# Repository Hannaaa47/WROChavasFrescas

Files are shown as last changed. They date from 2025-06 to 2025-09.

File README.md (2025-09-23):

<div align="center">

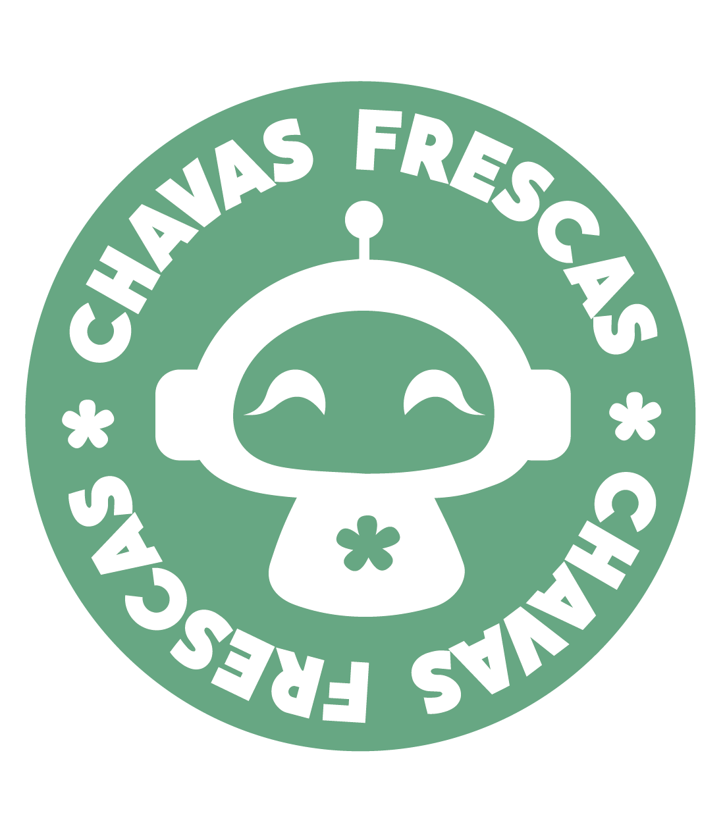
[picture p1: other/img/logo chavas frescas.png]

</div> 

<br>

En este repositorio nuestro equipo "Chavas frescas" desglosaremos como logramos crear un robot para participar en la World Robot Olympiad en la categoria de Future Engineers.

&nbsp;

# Tabla de contenidos
* **[Contenido del repositorio](#contenido-del-repositorio)**
* **[¿En que consiste la competencia?](#en-que-consiste-la-competencia)**
* **[Equipo](#equipo)**
* **[Fotos del robot](#fotos-del-robot)**
* **[Videos del robot](#videos-del-robot)**
* **[Hardware](#hardware)**
  * [Componentes](#componentes)
  * [Reporte de costos](#reporte-de-costos)
* **[Mobility Management](#mobility-management)**
  * [Diseño del chasis](#diseño-del-chasis) 
  * [Elección de motores](#eleccion-de-motores) 
* **[Power and Sense Management](#power-and-sense-management)**
  * [Voltaje y amperaje](#voltaje-y-amperaje) 
  * [Esquema](#esquema) 
  * [Sensores](#sensores) 
* **[Software](#software)**

&nbsp;

# Contenido del repositorio
  
*  [`models`](models) — contiene los modelos 3D de nuestro robot.

*  [`other`](other) — contiene imagenes y archivos que ayudan a entender más a fondo como preparar el robot para la competencia, contiene datasheets y imagenes de los componentes.

*  [`schemes`](schemes) — contiene el esquema de conexiones del robot y un diagrama de flujo del codigo.

*  [`src`](src) — contiene el codigo de nuestro robot.

*  [`t-photos`](t-photos) — continene fotos de los integrantes del equipo.

*  [`v-photos`](v-photos) — contiene seis fotos del carrito.

*  [`videos`](videos) — contiene un link para un video del robot.

&nbsp;

# ¿En que consiste la competencia?

La World Robot Olympiad es una competencia mundial de robótica que busca una competencia sana para jóvenes, alentando el aprendizaje y la curiosidad.

En nuestro caso participamos en la categoría de Future Engineers, el objetivo es construir un vehículo autodirigido con algunas limitaciones(como peso, tamaño y número de motores), el cual debe de ser capaz de pasar dos pruebas.

Prueba abierta.
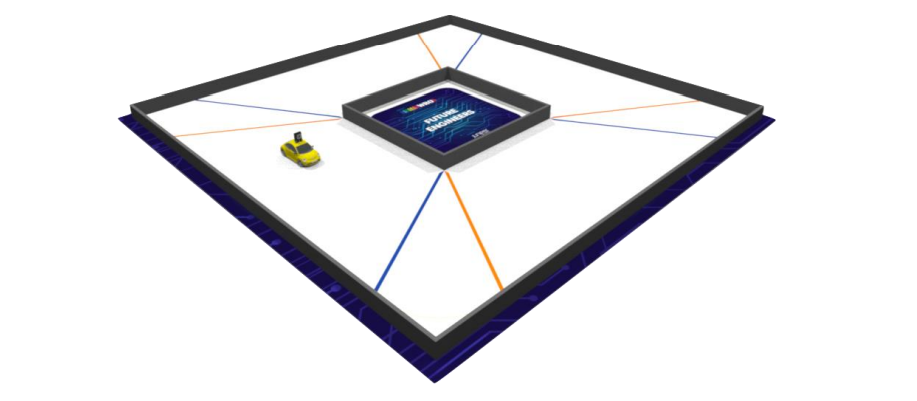
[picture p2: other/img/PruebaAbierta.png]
Prueba abierta


Prueba de obstáculos. 
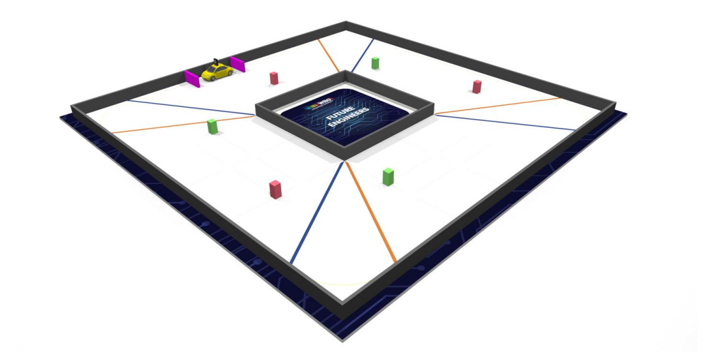
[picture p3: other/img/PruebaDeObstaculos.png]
Prueba de obstáculos


En la prueba abierta nuestro vehículo debe completar exitosamente tres vueltas a la pista. En la prueba de obstáculos además de dar tres vueltas a la pista el robot debe de ir esquivando obstáculos y al final estacionarse en paralelo. En ambas pruebas existen elementos aleatorios como la posición de los obstáculos y el sentido de las vueltas, estos elementos cambian después de cada ronda. Para conocer más puede leer las [reglas generales](https://wro-association.org/wp-content/uploads/WRO-2022-Future-Engineers-General-Rules.pdf) o visitar el [sitio oficial](https://wromexico.org/). 

&nbsp;

# Equipo

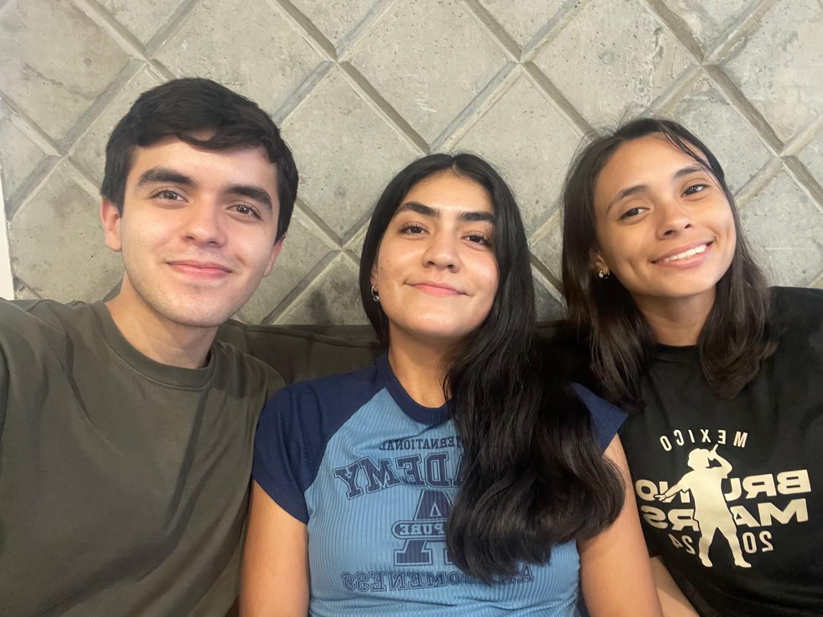
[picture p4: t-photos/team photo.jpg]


Integrantes del equipo:
- Hanna Alejandra Amador Sánchez
- Ilse Marianne Castillo Pimienta
- Yonatan Morales Togo

Asesor:
- Cesar Espinosa Arce
  
&nbsp;

# Fotos del robot

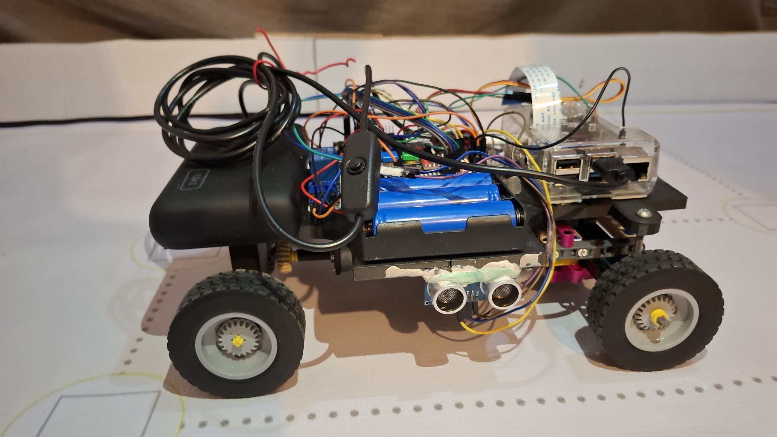
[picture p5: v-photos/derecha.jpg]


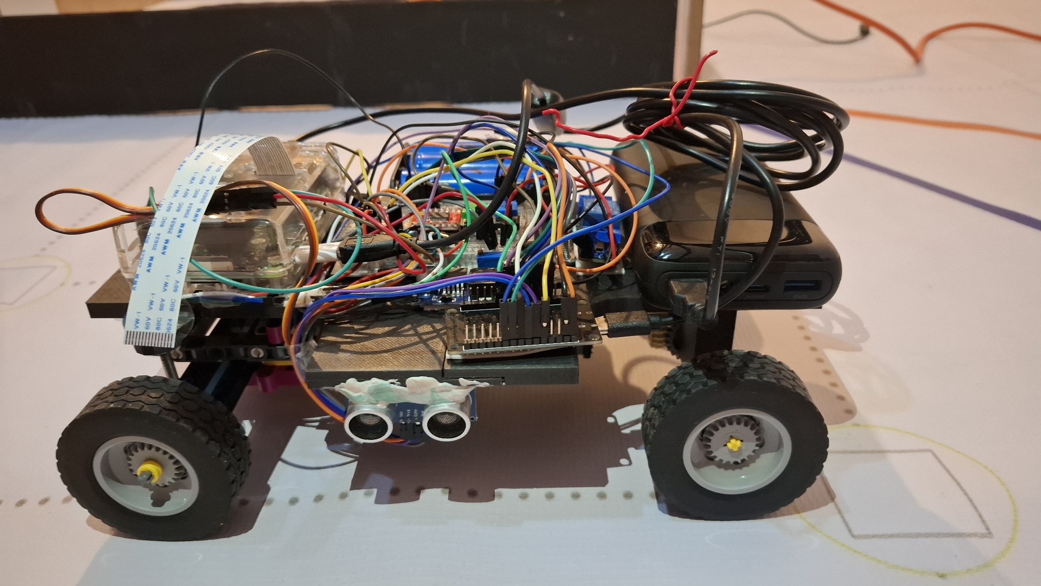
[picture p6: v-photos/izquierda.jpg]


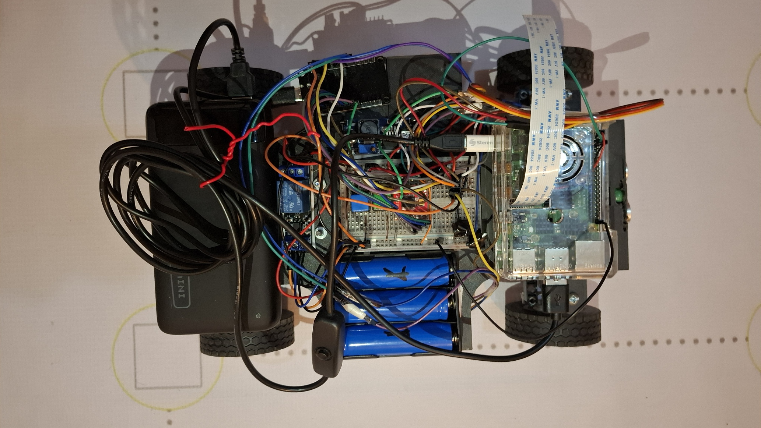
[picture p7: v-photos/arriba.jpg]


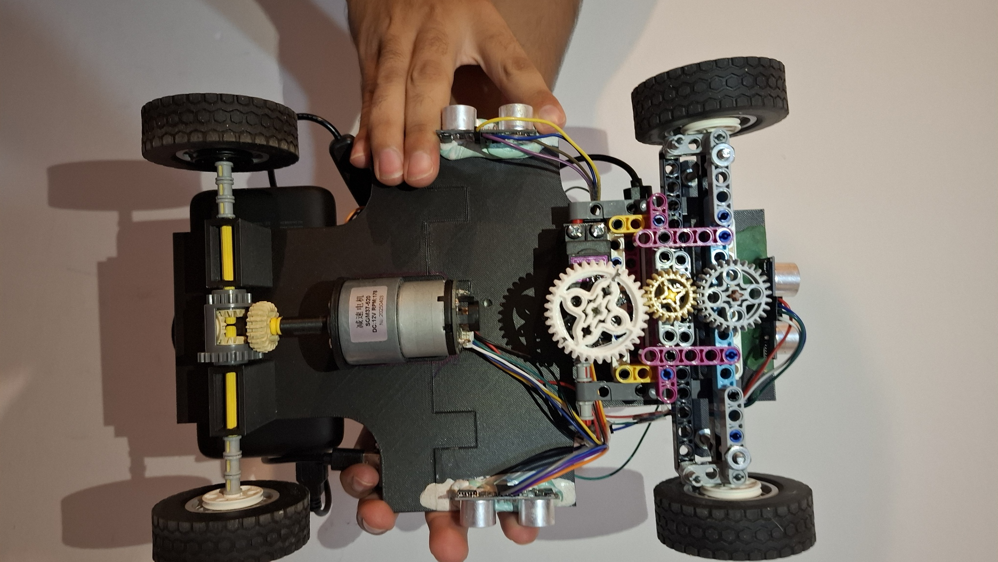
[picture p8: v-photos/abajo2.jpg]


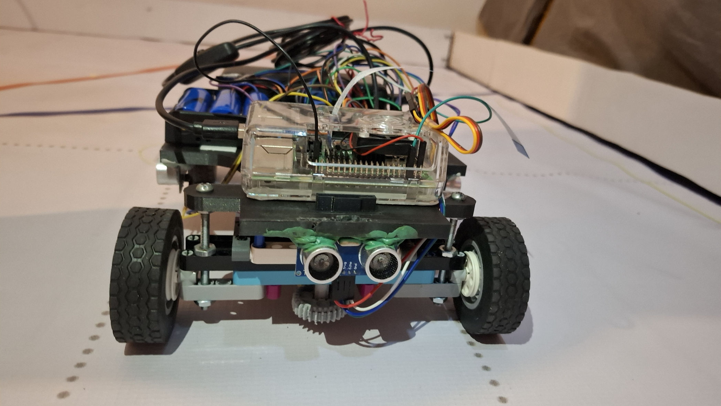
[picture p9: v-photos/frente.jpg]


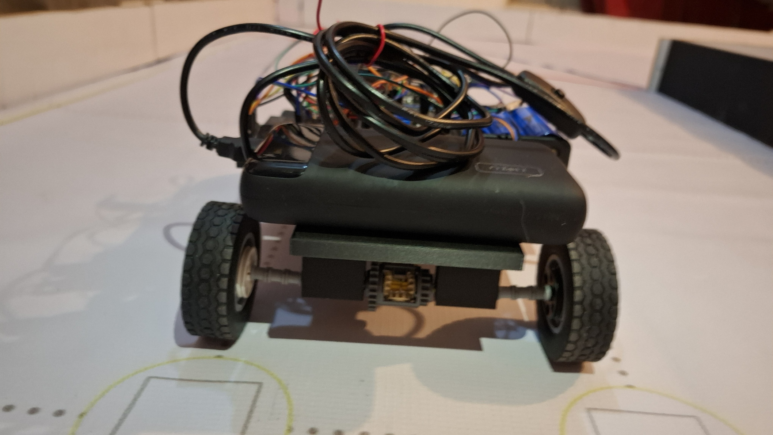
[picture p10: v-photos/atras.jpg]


&nbsp;  

# Videos del robot
Aqui esta el [link](https://youtu.be/UbjT6czdM9U?si=_D7zrM3F1YbVgJT3) para el video de nuestro robot.

# Hardware

## Componentes 

***Esp32*** 

Es un Single Board Microcontroller (SBM), es un sistema en chip (SoC) económico y de bajo consumo que combina funciones Wi-Fi y Bluetooth. Desde una perspectiva técnica, el ESP32 es un MCU de 32 bits con un microprocesador Tensilica Xtensa LX6, con una velocidad de reloj de hasta 240 MHz, 448 KB de ROM y 520 KB de SRAM. También incluye una amplia selección de periféricos, como un ADC de 10 bits, 6x PWM, I₂C, SPI, UART y más. La programación del ESP32 es relativamente sencilla, ya que admite diversos lenguajes de programación, como C/C++, ensamblador y Python. También es compatible con el IDE de Arduino, una popular plataforma de código abierto para la programación de microcontroladores. Para ver mas información puede ver el [datasheet](other/Datasheets/esp32-wrover_datasheet_en.pdf) y la descripción de los [pines GPIO](other/img/ESP32-Pinout.jpg).

Su función en nuestro proyecto es hacer de motor controller y obtener lecturas precisas de los sensores, dada a la rápida comunicación que tiene entre componentes. Elegimos al Esp32 sobre la opción clásica que sería algún arduino, ya que después de analizar ambos llegamos a la conclusión que el Esp32 es mejor. 
<table>
  <tr>
    <td style="width:400px; text-align:center; vertical-align:middle;">
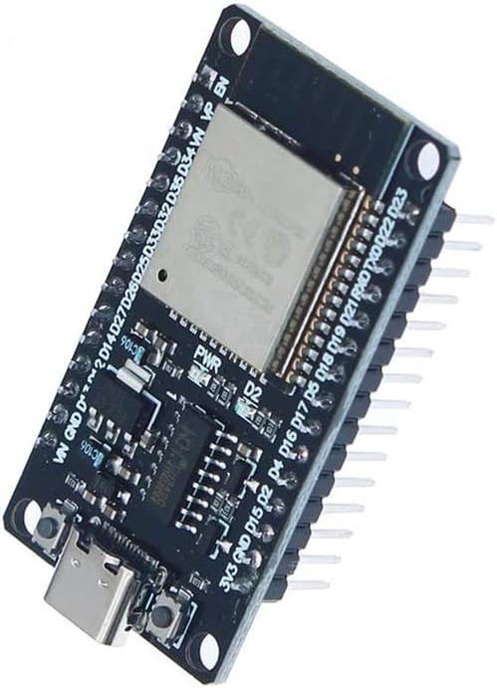
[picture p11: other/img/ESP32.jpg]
ESP32
      
    </td>
    <td style="width:500px; text-align:left; vertical-align:middle;">
      <h3>Especificaciones:</h3>
      <ul>
        <li>Voltaje: 2.3V ~ 3.6V</li>
        <li>Amperaje: 80mA ~ 250mA</li>
      </ul>
    </td>
  </tr>
</table>

<br>

***Raspberry Pi 4 Model B***

El Single-Board Computer (SBC), es un pequeño computador, consiste en una placa base que soporta distintos componentes de un ordenador, como un procesador ARM de hasta 1500 MHz, un chip gráfico y una memoria RAM de hasta 8 GB. Puede ver la configuración de los gpio pines en esta [imagen](other/img/pinesRaspberry.jpg), para ver más información consulte el [datasheet](other/Datasheets/raspberry-pi-4-product-brief.pdf).

Hace la función del cerebro principal del robot, esta a cargo de la computer vision interpretando los datos de la camara, ademas toma las decisiones importantes.

<table>
  <tr>
    <td style="width:400px; text-align:center; vertical-align:middle;">
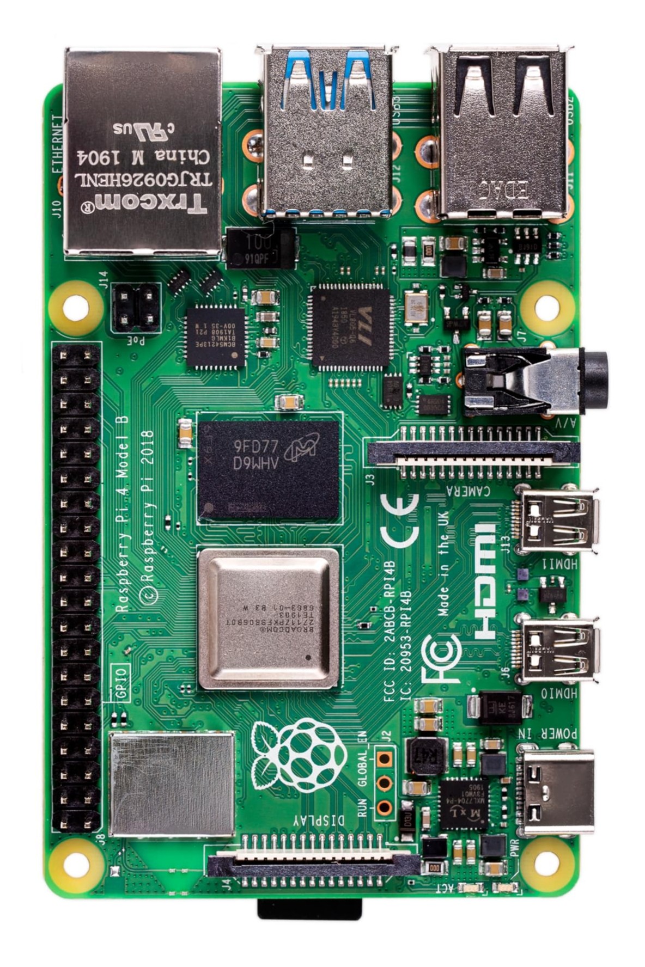
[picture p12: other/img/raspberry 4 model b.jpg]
Raspberry pi
      
    </td>
    <td style="width:500px; text-align:left; vertical-align:middle;">
      <h3>Especificaciones:</h3>
      <ul>
        <li>Voltaje: 5V</li>
        <li>Amperaje: 2500mA ~ 3000mA </li>
      </ul>
    </td>
  </tr>
</table>

<br>

***Servomotor MG995 180°***

Un servomotor es un tipo de motor que permite controlar con precisión la posición, velocidad y aceleración de su eje. A diferencia de un motor eléctrico convencional, un servomotor utiliza un sistema de retroalimentación (como un encoder) para monitorear y corregir continuamente su movimiento, logrando un control más exacto. 

Usamos este servomotor para controlar la dirección del carro, decidimos usar este modelo de servomotor devido a su gran torque. Para más información consulte el [datasheet](other/Datasheets/Servomotor_MG995_datasheet.pdf).

<table>
  <tr>
    <td style="width:400px; text-align:center; vertical-align:middle;">
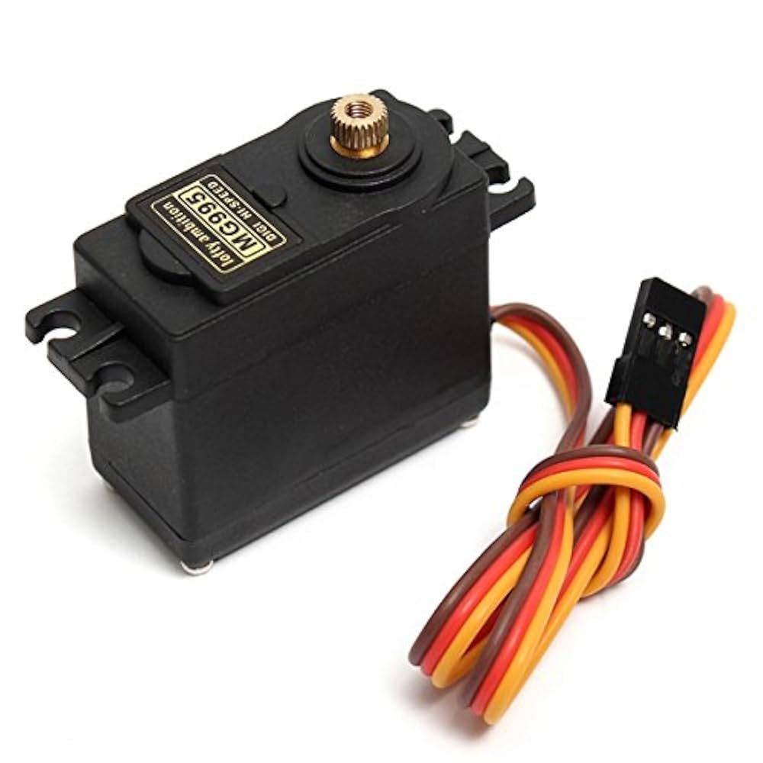
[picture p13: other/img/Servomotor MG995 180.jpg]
Servomotor
      
    </td>
    <td style="width:500px; text-align:left; vertical-align:middle;">
      <h3>Especificaciones:</h3>
      <ul>
        <li>Voltaje:  4.8V - 7.2V</li>
        <li>Amperaje: 200mA ~ 1200mA </li>
        <li>Torque: 9.4kg/cm (4.8V) - 11kg/cm (6V)</li>
      </ul>
    </td>
  </tr>
</table>
  
<br>

***Motor JGB37-520 DC 12v con encoder***

Elegimos un motor de corriente continua, debido a su facilidad para usarlo. Estos motores toman la energía eléctrica mediante corriente continua y la convierten en rotación mecánica. Despues de calcular el [torque](/research/README.md) concluimos que ibamos a necesitar un motor con un buen torque para poder mover el robot. 

Este motor tambien cuenta con un encoder, el encoder nos ayuda a monitorear las el moviemiento del motor.

// gracias a el pudimos implementar un sistema [PID](/research/README.md) para corregir las variaciones de la 
// energia y contar un moviemiento consistente. 
 
 Si quieres saber un poco más del motor revisa esta [imagen](other/Datasheets/motor.webp).

<table>
  <tr>
    <td style="width:400px; text-align:center; vertical-align:middle;">
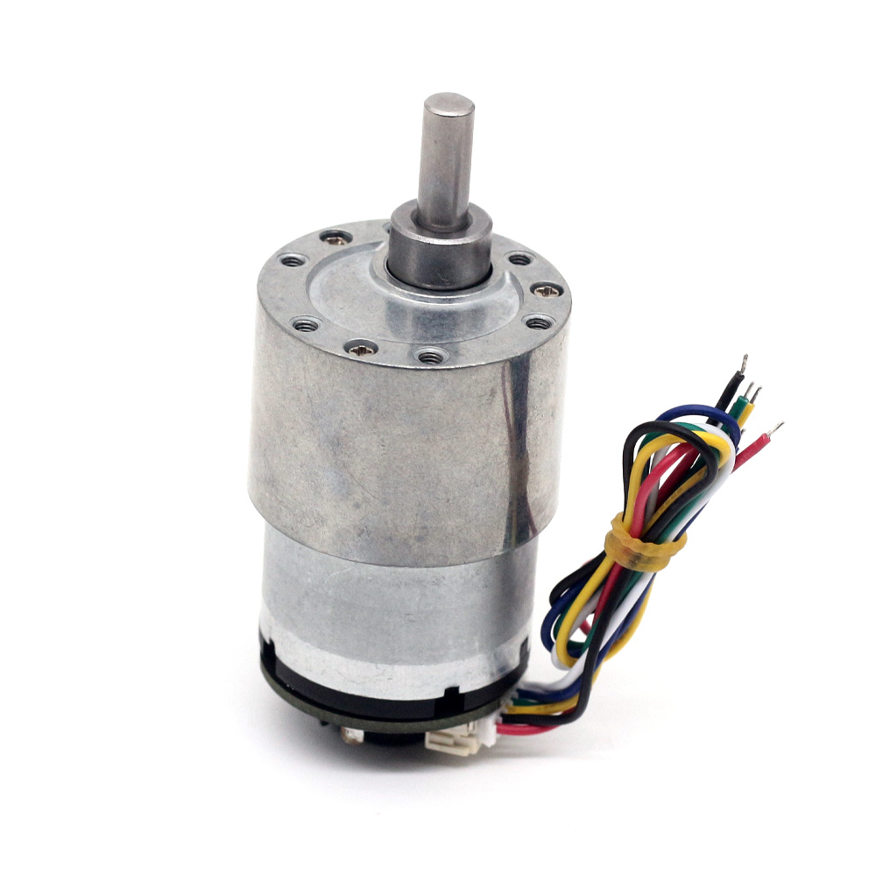
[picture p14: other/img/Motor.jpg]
Motor
      
    </td>
    <td style="width:500px; text-align:left; vertical-align:middle;">
      <h3>Especificaciones:</h3>
      <ul>
        <li>Voltaje:  12V</li>
        <li>Amperaje: 120mA ~ 2300mA </li>
        <li>Torque: 6.5kg.cm (120mA) - 9kg.cm (2300mA)</li>
        <h3>Encoder</h3>
        <li>Voltaje: 3.3V</li>
      </ul>
    </td>
  </tr>
</table>
  
<br>

***Motor driver TB6612FNG***

Un motor driver nos ayuda a controlar el motor con un voltaje más alto, controlando la velocidad y el sentido de giro. 

El driver para motores TB6612FNG posee dos puentes H, puede controlar hasta dos motores de DC con una corriente costante de 1.2A (3.2A pico). Dos señales de entrada (IN1 y IN2) pueden ser usadas para controlar el motor en uno de cuatro modos posibles: CW(giro en sentido de las manecillas del reloj), CCW (en contra de las manecillas), short-brake y stop. Las dos salidas de motores (A y B) pueden ser controladas de manera separada, la velocidad de cada motor es controlada mediante una señal PWM con una frecuencia de hasta 100kHz. El pin STBY cuando es puesto en HIGH coloca al motor en modo de standby. El driver posee diodos internos de protección.
Elegimos este motor driver debido a su gran eficiencia energética, su tamaño compacto, genera menos calor y su control preciso. Para saber más sobre este componente revise su [datasheet](other/Datasheets/TB6612FNG.pdf) y para ver el pinout vea la [imagen](other/img/tb6612fng-pinout.png).

<table>
  <tr>
    <td style="width:400px; text-align:center; vertical-align:middle;">
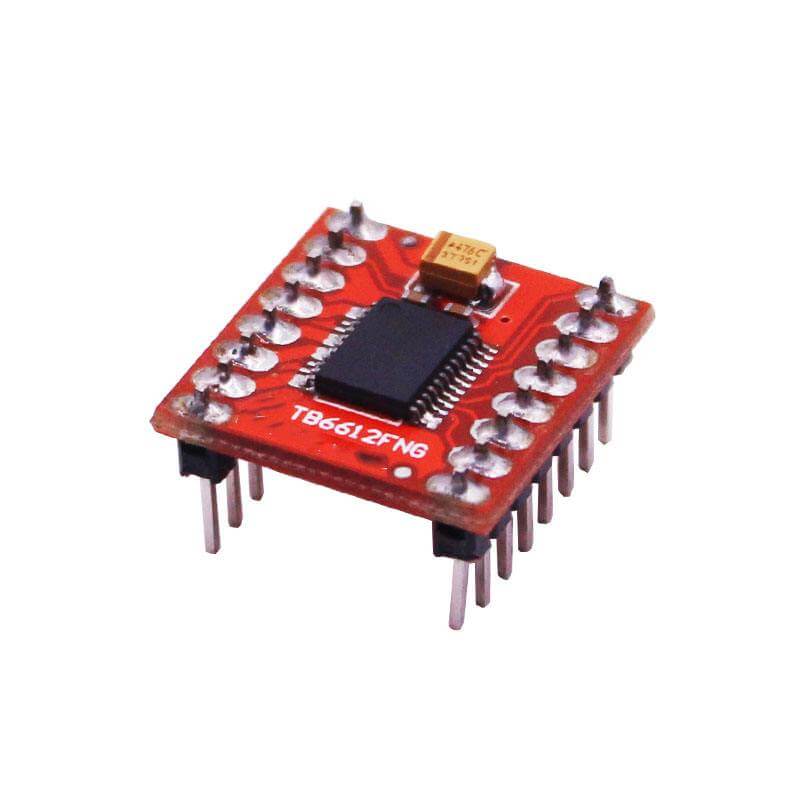
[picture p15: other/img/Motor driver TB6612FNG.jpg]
Motor driver
      
    </td>
    <td style="width:500px; text-align:left; vertical-align:middle;">
      <h3>Especificaciones:</h3>
      <ul>
        <li>Voltaje lógico (VCC): 2.7V - 5.5V</li>
        <li>Voltaje de motor (VM): 4.5V - 13.5V</li>
        <li>Corriente máxima por motor: 1.2A continuos / 3.2A pico</li>
      </ul>
    </td>
  </tr>
</table>
  
<br>

***Cámara OV5647***

Usamos una mini cámara gran angular, esta se conecta directamente al raspberry. Para conocer mas detalles de la cámara puede ver el [datasheet](other/Datasheets/ov5647_full.pdf).
  
<table>
  <tr>
    <td style="width:400px; text-align:center; vertical-align:middle;">
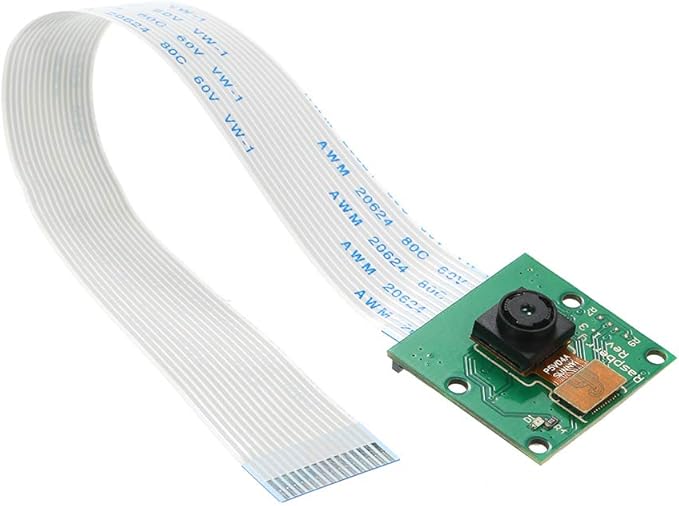
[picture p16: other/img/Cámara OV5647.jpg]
Camara
      
    </td>
    <td style="width:500px; text-align:left; vertical-align:middle;">
      <h3>Especificaciones:</h3>
      <ul>
        <li>Video: 1080p a 30fps</li>
        <li>Campo de visión: 2.0 x 1.33 m a 2 m</li>
      </ul>
    </td>
  </tr>
</table>
  
<br>

***Sensor Ultrasónico HC-SR04***

Los sensores de ultrasonidos o sensores ultrasónicos son detectores de proximidad que trabajan libres de roces mecánicos y que detectan objetos a distancias que van desde pocos centímetros hasta varios metros. El sensor emite una onda y mide el tiempo que la señal tarda en regresar. Más detalles en el [datasheet](other/Datasheets/HC-SR04-Ultrasonic.pdf).
En otras palabras el sensor ultrasónico nos permite saber con precision a que distancia se encuentran las paredes. 

<table>
  <tr>
    <td style="width:400px; text-align:center; vertical-align:middle;">
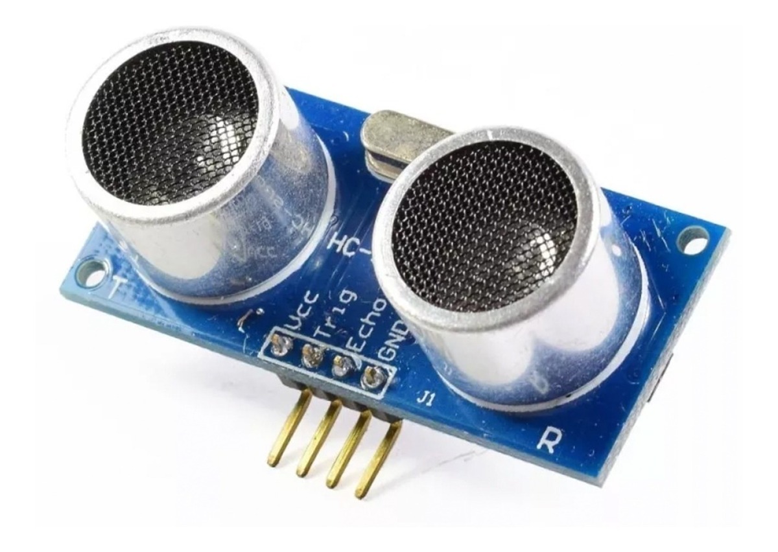
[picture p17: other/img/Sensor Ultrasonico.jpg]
Sensor ultrasonico
      
    </td>
    <td style="width:500px; text-align:left; vertical-align:middle;">
      <h3>Especificaciones:</h3>
      <ul>
        <li>Voltaje: 3.3V ~ 5V</li>
        <li>Amperaje: 15mA </li>
        <li>Rango: 2cm ~ 400cm </li>
      </ul>
    </td>
  </tr>
</table>
  
<br>
 
***Baterías 18650 3.7v 3000 mAh***

La pila 18650 es una batería recargable Li-ion, que se parece mucho a la pila tipo AA convencional. Para este proyecto usamos 3 baterias 18650 de 3.7V en serie para obtener un voltaje total de 11.1V.

<table>
  <tr>
    <td style="width:400px; text-align:center; vertical-align:middle;">
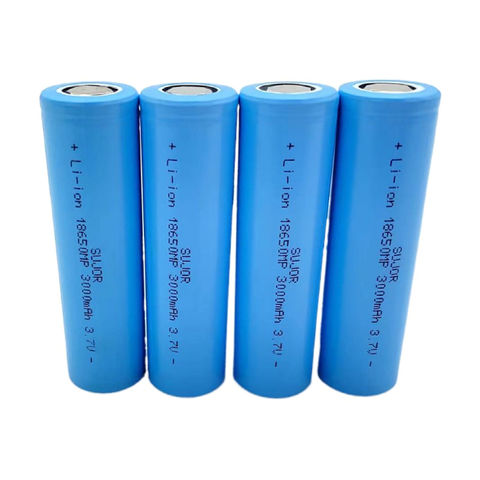
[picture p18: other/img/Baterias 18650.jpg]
Baterias
      
    </td>
    <<td style="width:500px; text-align:left; vertical-align:middle;">
      <h3>Especificaciones:</h3>
      <ul>
        <li>Voltaje: 3.7V</li>
        <li>Amperaje: 3000mA  </li>
        <li>Ciclos de vida: 300–500 ciclos </li>
      </ul>
    </td>
  </tr>
</table>
  
<br>
  
***LM2596 Regulador Step Down***

El LM2596 es un Regulador Step Down de 25W y 3A que ofrece una solución eficiente para reducir el voltaje de entrada en un circuito. Diseñado para manejar corrientes de hasta 3A, este regulador puede aceptar un voltaje de entrada que varía de 4 a 35V y proporciona un voltaje de salida ajustable de 2 a 28V. Gracias a su potenciómetro (trimpot) multivuelta, puedes seleccionar fácilmente el voltaje de salida deseado, lo que lo convierte en una opción versátil para una variedad de aplicaciones electrónicas.

<table>
  <tr>
    <td style="width:400px; text-align:center; vertical-align:middle;">
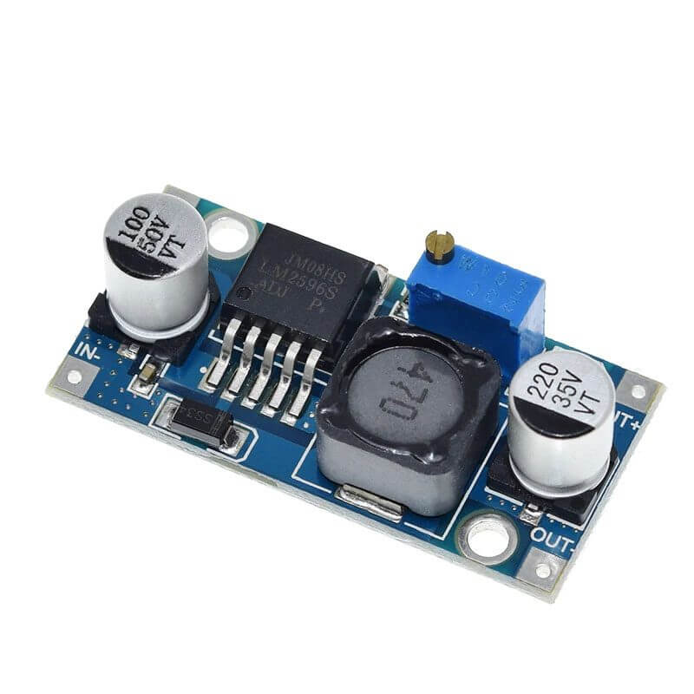
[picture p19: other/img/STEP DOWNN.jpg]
step down
      
    </td>
    <td style="width:500px; text-align:left; vertical-align:middle;">
      <h3>Especificaciones:</h3>
      <ul>
        <li>Voltaje de entrada: 4V-35V</li>
        <li>Voltaje de salida: 2V-30V </li>
        <li>Corriente de salida máxima: 3A</li>
      </ul>
    </td>
  </tr>
</table>
  
<br>

## Reporte de costos
<div align="left">

<table>
  <thead>
    <tr>
      <th align="center">Nombre</th>
      <th align="center">Cantidad</th>
      <th align="center">Costo</th>
    </tr>
  </thead>
  <tbody>
    <tr>
      <td>ESP32</td>
      <td>1</td>
      <td align="center">$200.00</td>
    </tr>
    <tr>
      <td>Raspberry Pi 4 Model B</td>
      <td>1</td>
      <td align="center">$2100.00</td>
    </tr>
    <tr>
      <td>Servomotor MG995 180°</td>
      <td>1</td>
      <td align="center">$155.00</td>
    </tr>
    <tr>
      <td>Motor JGB37-520 DC 12v con encoder</td>
      <td>1</td>
      <td align="center">$258.00</td>
    </tr>
    <tr>
      <td>Motor driver TB6612FNG</td>
      <td>1</td>
      <td align="center">$96.50</td>
    </tr>
    <tr>
      <td>Cámara OV5647</td>
      <td>1</td>
      <td align="center">$160.00</td>
    </tr>
    <tr>
      <td>Sensor Ultrasónico HC-SR04</td>
      <td>3</td>
      <td align="center">$49.00</td>
    </tr>
    <tr>
      <td>6 Baterías 18650 3.7v 3000 mAh con cargador</td>
      <td>1</td>
      <td align="center">$493.05</td>
    </tr>
    <tr>
      <td>LM2596 Regulador Step Down 25W 3A</td>
      <td>1</td>
      <td align="center">$60.00</td>
    </tr>
    <tr>
    <tr>
      <td>Botones</td>
      <td>1</td>
      <td align="center">$60.00</td>
    </tr>
    <tr>
    <tr>
      <td>Adaptador</td>
      <td>1</td>
      <td align="center">$40.00</td>
    </tr>
    <tr>
    <tr>
      <td><strong>Total</strong></td>
      <td></td>
      <td align="center"><strong>$3671.5</strong></td>
    </tr>
  </tbody>
</table>

</div>

+ impresion 3d y 
otras cosas..

&nbsp;

# Mobility Management

## Diseño del chasis

Nuestro carro es de tracción trasera, funciona con un motor de 12v que, con adaptador del motor a lego, transmite el movimiento a las llantas traseras. En la parte delantera para el sistema de giro optamos por un sistema sencillo, sin Ackermann. Adaptamos un soporte especial para la cámara, para el motor y para el servo. Los ultrasónicos los pegamos con plastiloka por facilidad.

Para realizar el diseño del chasis tuvimos muchas complicaciones. Primero hicimos un primer prototipo con plástico y tapas de garrafón como llantas, nos sirvió para darnos una idea de cómo deberían de funcionar los ejes, pero era muy frágil. Nuestro siguiente prototipo fue con madera y tornillos, pero las medidas no eran muy precisas y adaptarlo exactamente a los componentes electrónicos iba a ser muy complicado. Por lo que pasamos a hacer un modelo 3D, para realizar este modelo usamos Solidworks, todos los modelos se encuentran en la carpeta de [modelos](models). Pero al momento de imprimirlos en 3D no se pudieron imprimir bien los círculos en general, y el sistema de giro del carro era muy inestable. Por último, para solucionar lo del sistema de giro usamos legos y un engranaje modelado en 3D para que encaje correctamente con las demás piezas de lego.

<br>

## Eleccion de motores 
Las dimensiones maximas de nuestro robot son de 30x20x30 cm y 1.5 kg, basandonos en eso elegimos nuestros componentes, intentamos usar los motores basicos, como el motor amarillo y el servo chico normal, pero no tenian el suficiente poder.

**Motor JGB37-520 DC 12v** 

Este motor cuentan con un Torque: 6.5kg.cm (120mA) - 9kg.cm (2300mA), lo que es mas que suficiente para poder mover el robot. El robot pesa 1.3kg, muy por debajo del minimo de peso que este motor puede mover, gracias a esto obtenemos bastante poder de movimiento. 
Anteriormente se intento con un motorreductor, que tiene un torque de salida de 1.1kg a 5 volts, algo que es insuficiente para poder mover el peso del robot anteriormente mencionado de 1.3 kg. 

**Motor driver TB6612FNG**

Se escogio este motor driver, porque al hacer una investigacion, se concluyo que es mejor que el motor driver l298n, porque este pierde energia, haciendo quno sea tan eficiente Como llega a ser con el TB6612FNG. 
Ademas que es mucho mas compacto que el l298n, ocupando menor espacio.

**Servomotor MG995 180°** 
 
Porque su torque es de 9.4kg por cm, esto siendo mas que suficiente para su movimiento, ya que el peso del robot es de 1.3kg. Se uso anteriormente un micro servo, pero no fuel suficientemente fuerte para mover el mecanismo.

&nbsp;

# Power and Sense Management

## Voltaje y amperaje

Para encender todo, se tiene que encender el switch que esta conectado a la pila portatil, encendiendo el raspberry. La pila portatil da 5V y3A al raspberry. Y con la salida del raspberry de 5V, alimenta al ESP32. El ESP32 tiene un relay  con su bobina conectada para energizarse. Este relay, esta abierto con el comun conectado a las 3 pilas de 4V, dando 12V en serie. La senal esta conectada a tierra, que en el momento en que se energiza el raspberry, luego el ESP32, ya se cierra el circuito y da tierra al relay, cerrando su circuito, dejando pasar la energia de las 3 pilas. Estas 3 pilas energizan al motor de 12V, y ademas, esta conectado a un step down que baja el voltaje a 5V, conectando el servo y los ultrasonicos. Asi se queda energizado todo con un solo switch.

## Esquema  

Creamos un diagrama del circuito en fritzing.
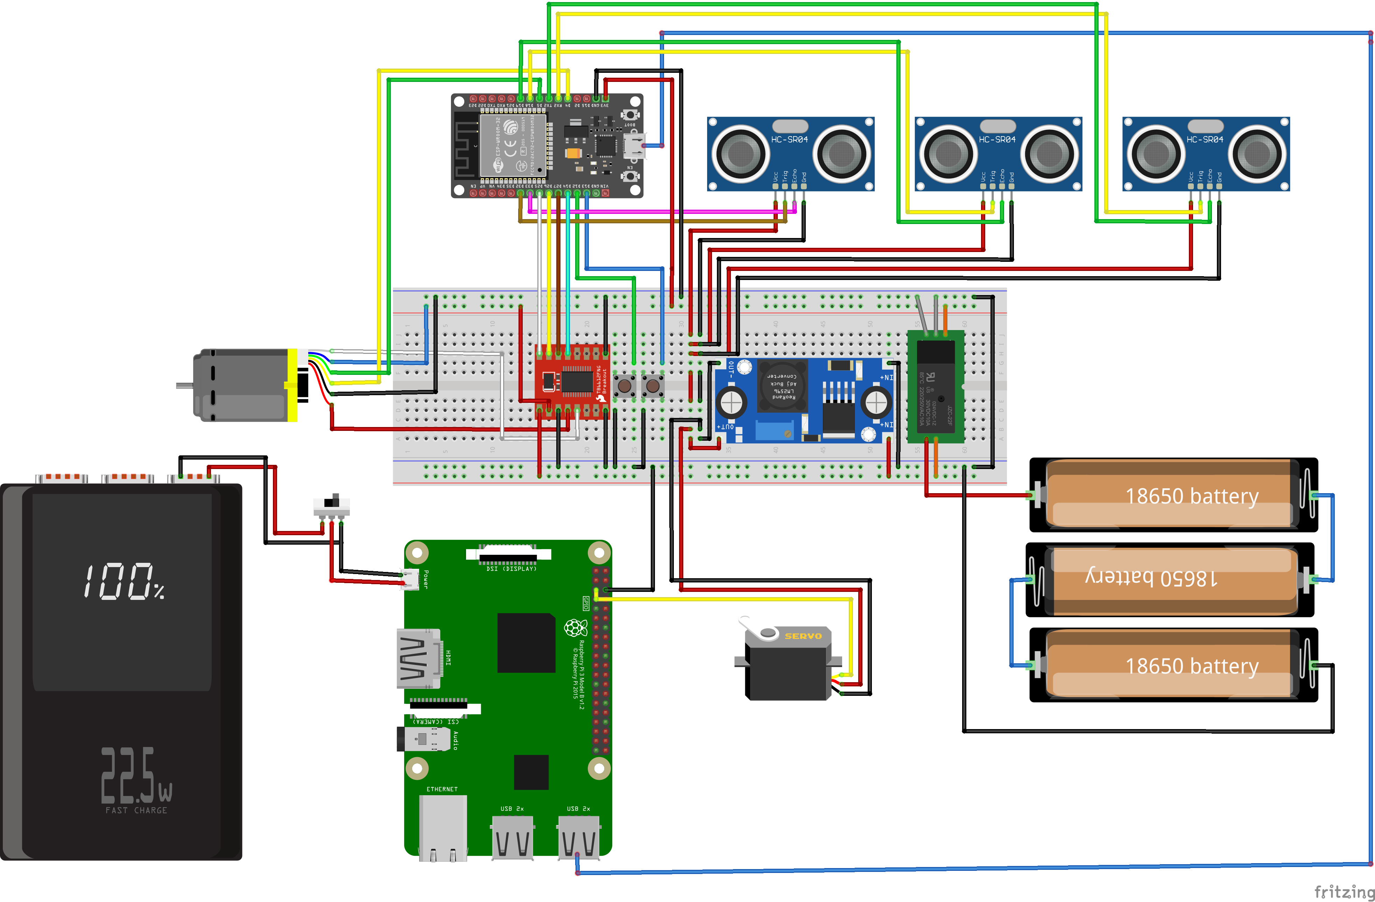
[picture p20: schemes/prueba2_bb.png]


<br>

## Sensores 

***Sensor Ultrasónico HC-SR04***

Este sensor lo estamos usando para saber a que distancia esta la pared, para que el robot reaccione de manera en que no choque. 
Los sensores ultrasónicos funcionan emitiendo ondas sonoras de alta frecuencia (más de 20 kHz) mediante un transductor piezoeléctrico. Estas ondas se reflejan al chocar con un objeto y regresan al sensor. El sensor mide el tiempo que tarda el eco en volver y calcula la distancia al objeto usando la fórmula:

Distancia = (T × C) / 2,
donde T es el tiempo y C la velocidad del sonido. La división entre dos se debe a que el tiempo incluye el recorrido de ida y vuelta.

***Cámara***

La usamos para poder detectar los obstaculos y su color. Esta hecha para su uso en el raspberry.

&nbsp;

# Software

Para el desarrollo de software programamos el Esp32 con Arduino Ide en C++, ademas usamos un Raspberry pi con programación en en python.
Para crear el codigo desarrollamos un programa en el cual el Esp32 lleva la logica principal del programa por su velocidad de lectura de los sensores, y el Raspberry pi solo se encarga de obedecer las instrucciones del otro microcontrolador. 
Usamos un filtro para las lecturas de los ultrasonicos y gravias a ellos detectamos las paredes. Ademas creamos uns state mechine para que fuera mas fail para el Esp32 llevar las cosas y que no se atrase.

&nbsp;

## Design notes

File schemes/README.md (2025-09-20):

Diagramas electricos
====

En este repositorio se puede consultar un diagrama electrico de nuestro circuito, ademas de los archivos necesarios para abrirlo en el fritzing.

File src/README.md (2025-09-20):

Control del software
====

Este repositorio contiene todo el codigo necesario para hacer a nuestro robot funncionar, contando con un apartado para el Esp32 y otro para el Raspberry pi.

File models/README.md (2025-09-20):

Modelos
====

En este directorio puedes ver todos los modelos 3d que usamos para nuestro robot.

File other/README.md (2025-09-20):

Otros
====

En esta carpeta podemos encontrar diversas imagenes, principalmente son imagenes de los componentes electronicos que ocupa nuestro robot, ademas de los datesheet de los mismos, con detalles tecnicos que nos fueron de mucha ayuda durante la realizacion del proyecto.

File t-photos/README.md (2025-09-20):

Fotos del equipo
====

Esta carpeta contiene dos imganes del equipo, una foto oficial y otra chistosa con nuestro amuleto de la suerte.

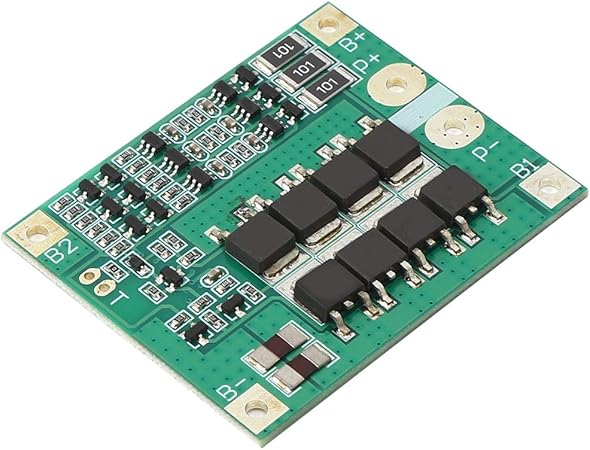
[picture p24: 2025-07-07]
other/img/Modulo de proteccion FTVOGUE 3S 12V.jpg

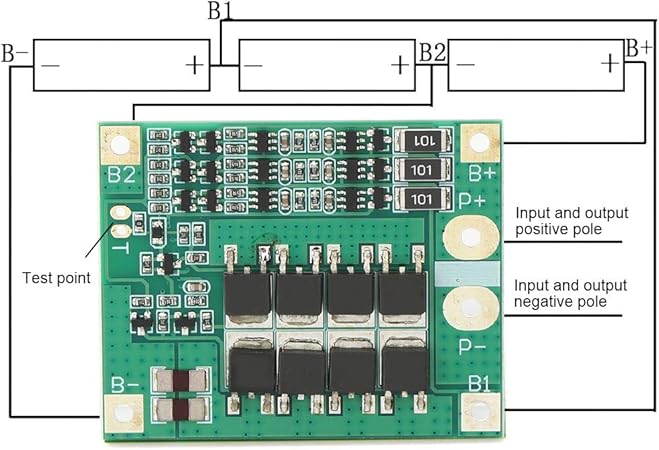
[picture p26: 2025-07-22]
other/img/bms detalles.jpg

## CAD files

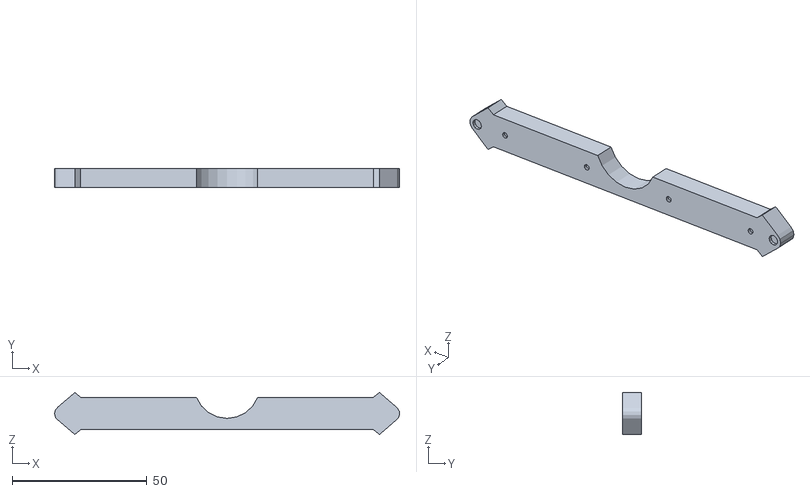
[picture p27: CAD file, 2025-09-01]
models/ENSAMBLE DE PIEZA MEDIO.STL
128.0 x 7.00 x 15.6

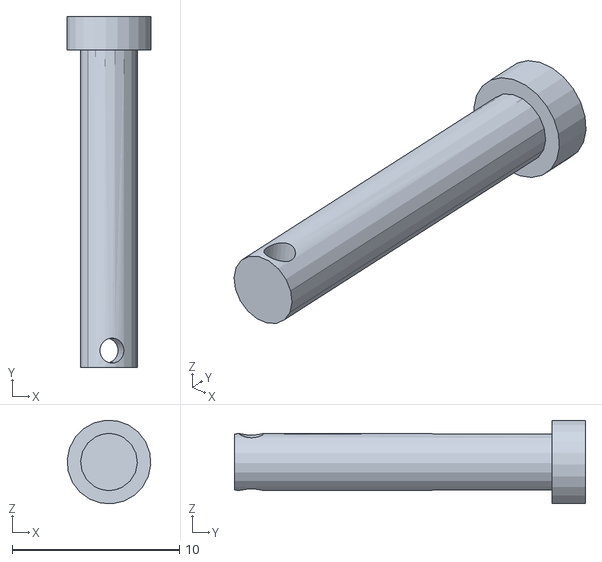
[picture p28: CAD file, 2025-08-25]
models/ENSAMBLE FINAL - CLAVO 17 MM-1.STL
5.00 x 21.0 x 5.00

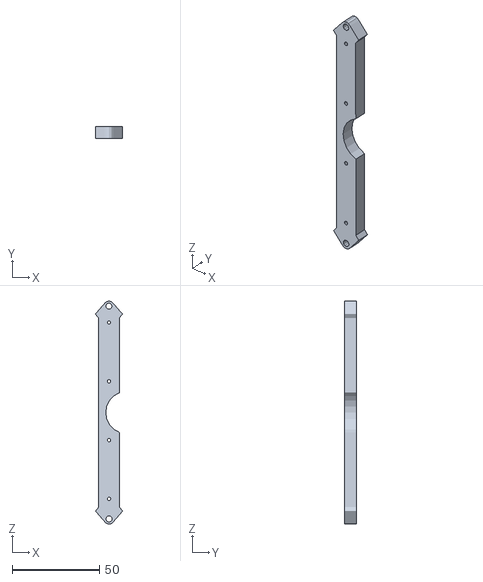
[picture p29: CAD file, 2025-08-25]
models/ENSAMBLE FINAL - ENSAMBLE DE PIEZA MEDIO-1.STL
15.7 x 7.00 x 127.9

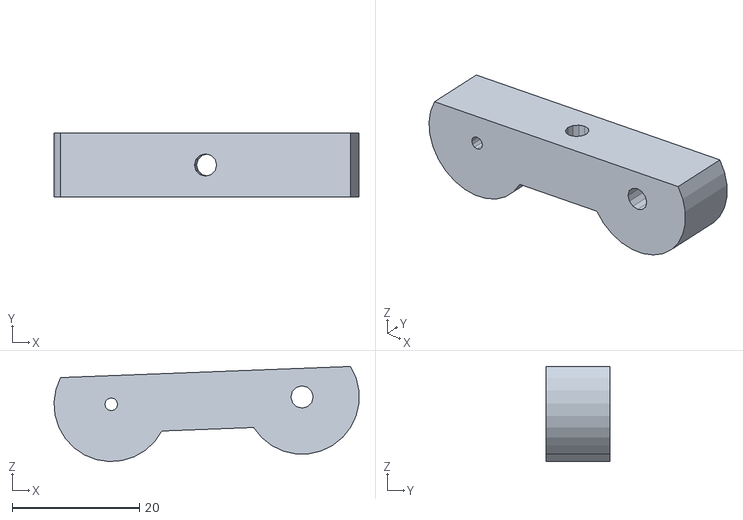
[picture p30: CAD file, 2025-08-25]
models/ENSAMBLE FINAL - UNIDOR DE ACKERMAN-1.STL
47.9 x 10.00 x 14.9

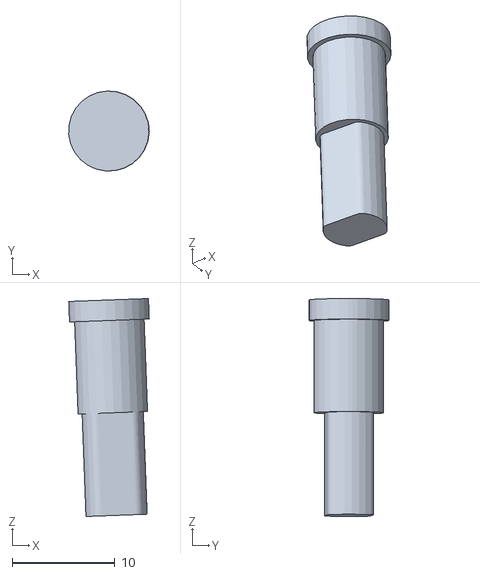
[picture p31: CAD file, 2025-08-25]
models/ENSAMBLE FINAL - GIRA PARA LLANTA NORMAL-1.STL
7.85 x 7.78 x 21.2

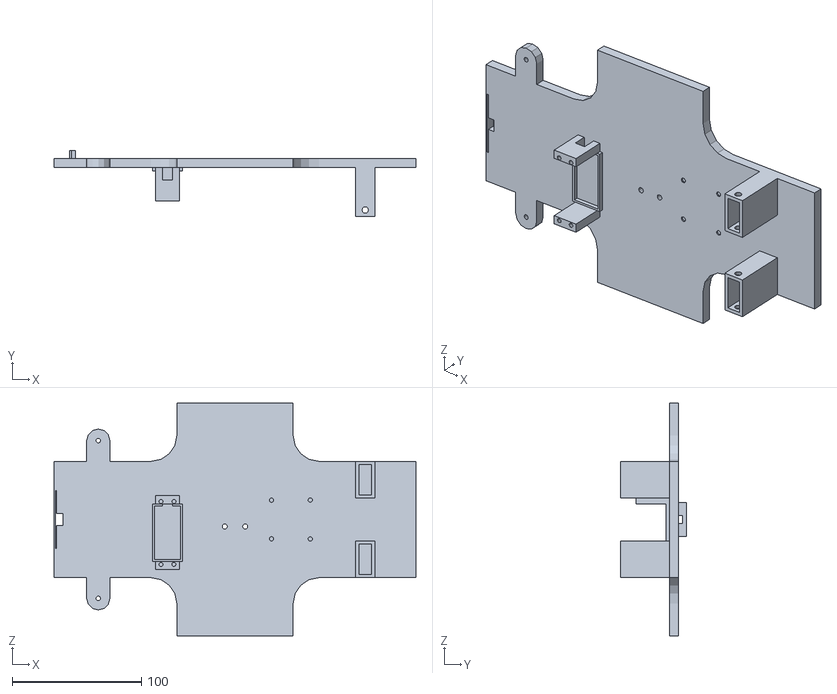
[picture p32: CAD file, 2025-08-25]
models/ENSAMBLE FINAL - PROTOTIPO PARA WRO-1.STL
280.0 x 51.0 x 180.0

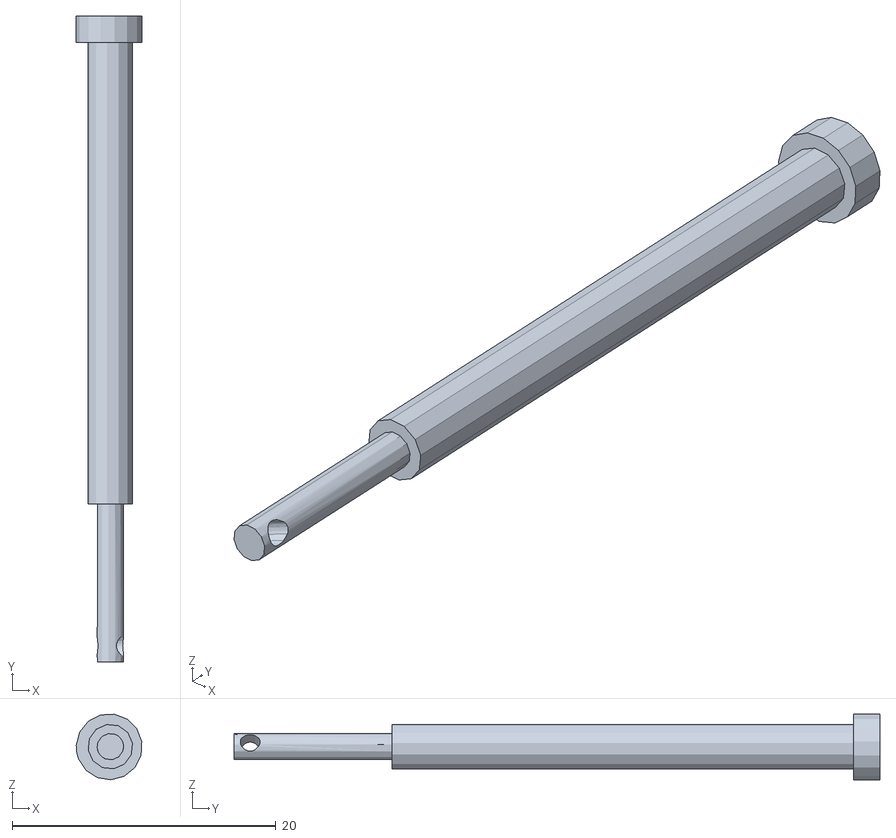
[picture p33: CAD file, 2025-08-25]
models/ENSAMBLE FINAL - clavo-2.STL
4.97 x 49.0 x 4.98

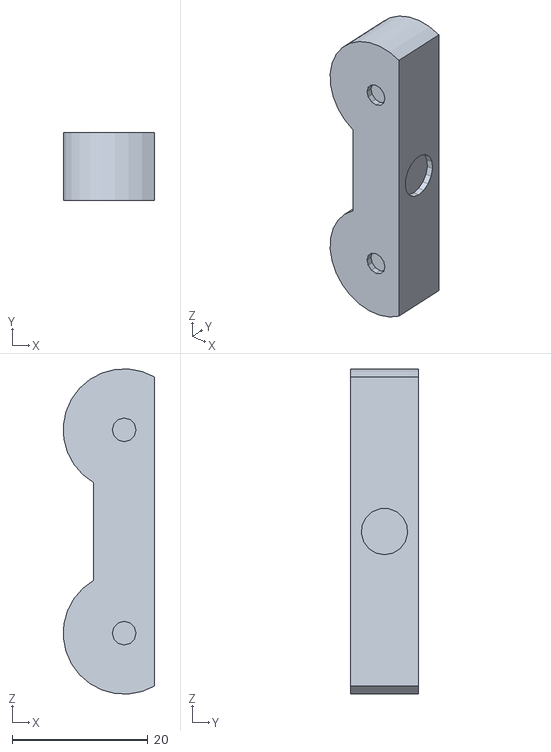
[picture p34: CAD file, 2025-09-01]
models/UNIDOR DE STEERING.STL
13.5 x 10.0 x 47.9

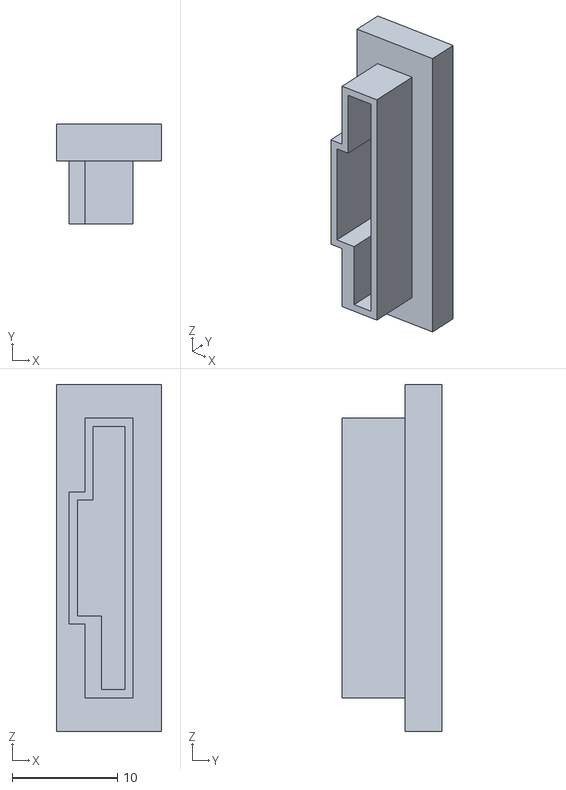
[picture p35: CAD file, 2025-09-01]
models/BASE PARA CAMARA.STL
10.0 x 9.50 x 33.0

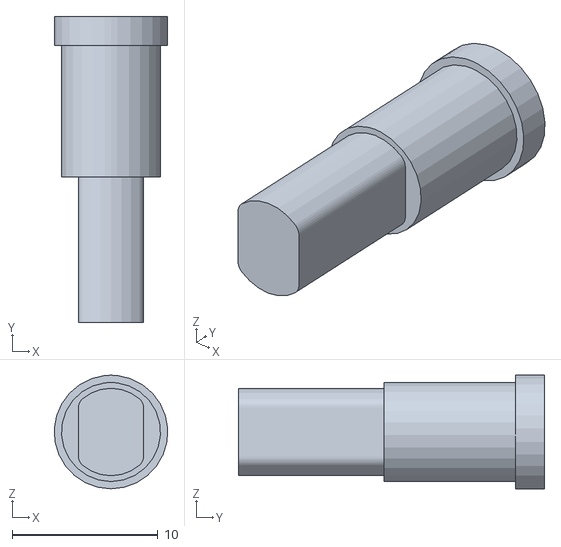
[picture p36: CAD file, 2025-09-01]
models/GIRA PARA LLANTA NORMAL.STL
7.79 x 21.0 x 7.80

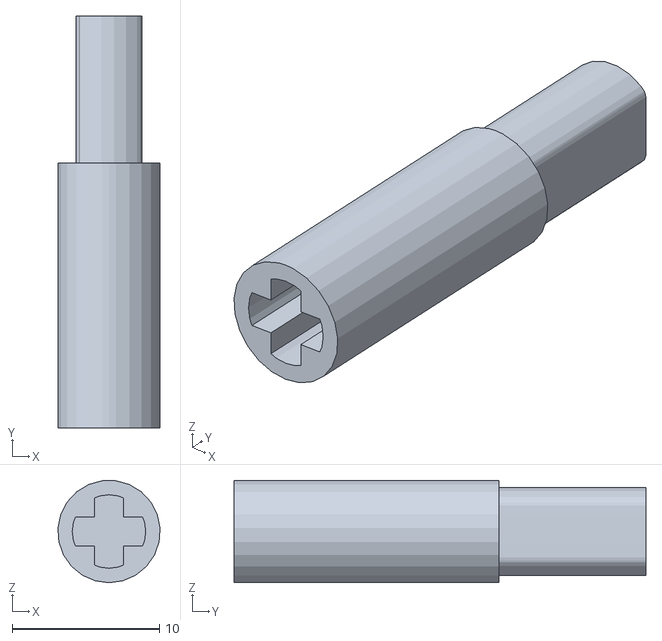
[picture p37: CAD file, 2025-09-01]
models/ADAPTADOR LEGO LLANTA STEREN.STL
6.94 x 28.0 x 6.96

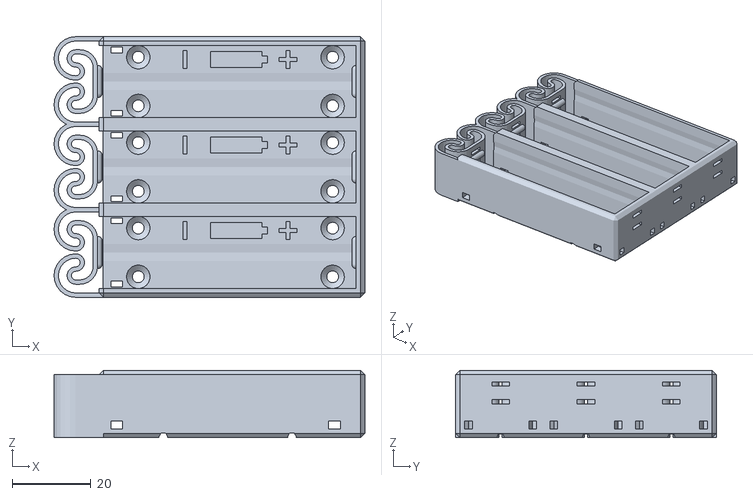
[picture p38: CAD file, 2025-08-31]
models/flexbatter18650x3.stl
79.2 x 66.4 x 17.2

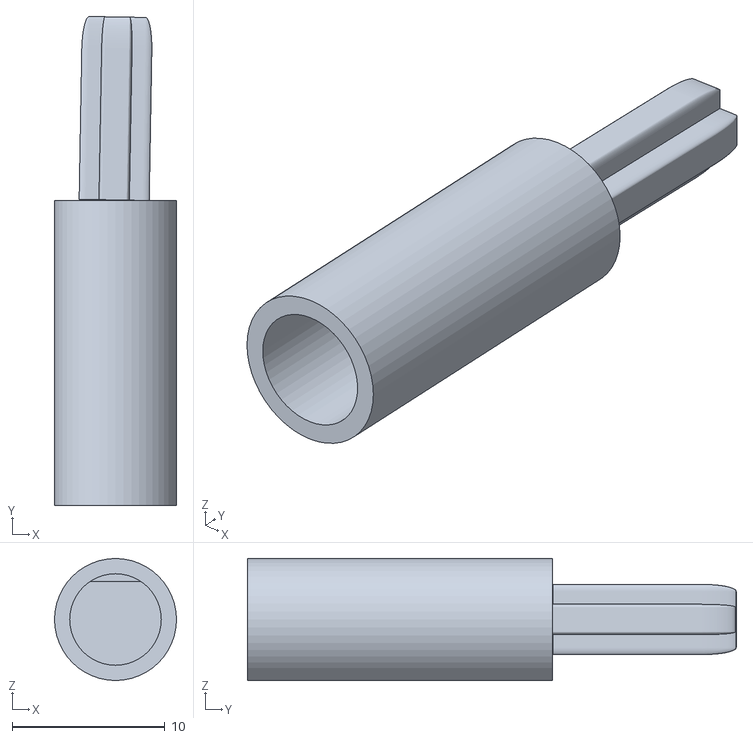
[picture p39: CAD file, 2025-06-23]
models/Copy of Lego Technic Axle 7 1.stl
8.00 x 32.1 x 8.00

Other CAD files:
models/ENSAMBLE FINAL - CLAVO 17 MM-2.STL
models/ENSAMBLE FINAL - GIRA PARA LLANTA NORMAL-2.STL
models/ENSAMBLE FINAL - UNIDOR DE ACKERMAN-2.STL
models/ENSAMBLE FINAL - clavo-1.STL

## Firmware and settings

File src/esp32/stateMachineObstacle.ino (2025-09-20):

#include "I2Cdev.h"
#include "math.h"

// ===== MOTOR =====
const int PIN_PWMA = 25;
const int PIN_IN1A = 26;
const int PIN_IN2A = 27;
const int PIN_STBY = 14;

// ===== ENCODER =====
const int PIN_ENCA = 5;
const int PIN_ENCB = 4;

// ===== BOTONES =====
const int PIN_BOTON_VERDE = 12;
const int PIN_BOTON_AZUL = 13;

// ===== ULTRASONICOS =====
// Frente
const int PIN_TRIG_FRENTE = 32;
const int PIN_ECHO_FRENTE = 33;
// Derecha
const int PIN_TRIG_DER = 18;
const int PIN_ECHO_DER = 19;
// Izquierda
const int PIN_TRIG_IZQ = 16;
const int PIN_ECHO_IZQ = 17;

#define MAX_DISTANCE 700
float timeOut = MAX_DISTANCE * 60;
int soundVelocity = 340;

// ===== VARIABLES =====
int posEncoder = 0;
float dEncoder = 0;
float dFrente = 0, dDer = 0, dIzq = 0;
float dfFrente = 0, dfIzq = 0, dfDer = 0;
float alpha = 0.7;
bool BV = false, BA = false;
int E = 0, B = 0, M = 0, U = 0, I = 0;
const int VELOCIDAD_NORMAL = 120;
char obstaculo = 'Y';

// -------------- Variables state machine
enum State { INICIO, AVANZAR_ABIERTA, SENTIDO_ABIERTA, GIRAR_ABIERTA, AVANCE_FINAL_ABIERTA, DETENERSE_ABIERTA, 
                    AVANZAR_OBSTACULOS, SENTIDO_OBSTACULOS, GIRAR_OBSTACULOS, ESQUIVA_OBSTACULOS,  AVANCE_FINAL_OBSTACULOS, DETENERSE_OBSTACULOS};

State currentState = INICIO;

//variables de la prueba
int distance = 100000;
int vueltas = 0;
int turns = 12;
unsigned long t_s1_v = 0;
unsigned long t_0_s1_v = 0;
int vuelta_delay = 5000;
int velocidad = 150;
bool fin = false;
int sentido = -1;

void setup() {
  Serial.begin(9600);
  setupMotor();
  setupEncoder();
  setupBotones();
  setupUltrasonicos();
}

void loop() {
  stateMachine();
  actualizarDistancias();
}

void stateMachine() {
  switch (currentState) {
    case INICIO:
      BotonVerdePresionado();
      BotonAzulPresionado();
      if (BV) {
        girarServo(1);
        delay(4000);
        girarServo(0);
        delay(4000);
        currentState = AVANZAR_ABIERTA;
        Serial.println("AVANZA_ABIERTA");
        resetEncoder();
      } else if (BA){
        girarServo(1);
        delay(4000);
        girarServo(0);
        delay(4000);
        currentState = AVANZAR_OBSTACULOS;
        Serial.println("AVANZAR_OBSTACULOS");
        resetEncoder();
      }
      break;

    case AVANZAR_ABIERTA:
      controlMotor(1);
      if (vueltas != 0) {
        if (sentido == -1) {
          if (dfDer > 30) {
            Serial.println("corrige derecha");
            girarServo(2);
            delay(100);
          }
          else if (dfDer < 20) {
            Serial.println("corrige izquierda");
            girarServo(-2);
            delay(100);
          } else {
            girarServo(0);
            delay(100);
          }
        } else {
          if (dfIzq > 30) {
            Serial.println("corrige izquierda");
            girarServo(-2);
          } else if (dfIzq < 20) {
            Serial.println("corrige derecha");
            girarServo(2);            
          } else {
            girarServo(0);
          }
        }
      }
      if (vueltas == 0 && dfFrente<45) {
        currentState = SENTIDO_ABIERTA;
        Serial.println("SENTIDO_ABIERTA");
        break;
      }
      if (dfFrente < 45 && dEncoder > 170) {
        giraAbierta();  
      }
      break;

    case SENTIDO_ABIERTA:
      mostrarDistancias();
      if (dfDer > dfIzq){
        sentido = 1;
      }else{
        sentido = -1;
      }
      currentState = GIRAR_ABIERTA;
      giraAbierta();
      break;

    case GIRAR_ABIERTA:
      Serial.print("encoder ");
      Serial.println(dEncoder);
      if (true) {
        vueltas++;
        resetEncoder();
        Serial.println(vueltas);
        if (vueltas >= turns) {
          currentState = AVANCE_FINAL_ABIERTA;
          Serial.println("AVANCE_FINAL_ABIERTA");
        } else {
          currentState = AVANZAR_ABIERTA;
          Serial.println("AVANZA_ABIERTA");
        }
      }
      break;

    case AVANCE_FINAL_ABIERTA:
      controlMotor(1);
      girarServo(0);
      if (dEncoder > 50) {
        currentState = DETENERSE_ABIERTA;
        Serial.println("DETENERSE_ABIERTA");
      }
      break;

    case DETENERSE_ABIERTA:
      controlMotor(0);
      break;

    case AVANZAR_OBSTACULOS:
      controlMotor(1);
      if (vueltas == 0 && dfFrente<65) {
        currentState = SENTIDO_OBSTACULOS;
        Serial.println("SENTIDO_OBSTACULOS");
        break;
      }


      if (vueltas != 0) {
        if (sentido == -1) {
          if (dfDer > 50) {
            Serial.println("corrige derecha");
            girarServo(2);
            delay(100);
          }
          else if (dfDer < 35) {
            Serial.println("corrige izquierda");
            girarServo(-2);
            delay(100);
          } else {
            girarServo(0);
            delay(100);
          }
        } else {
          if (dfIzq > 50) {
            Serial.println("corrige izquierda");
            girarServo(-2);
          } else if (dfIzq < 35) {
            Serial.println("corrige derecha");
            girarServo(2);            
          } else {
            girarServo(0);
          }
        }
      }
      
      if (dfFrente < 65) {
        giraObstaculos();  
      }
      break;
  
    case SENTIDO_OBSTACULOS:
      mostrarDistancias();
      if (dfDer > dfIzq){
        sentido = 1;
      }else{
        sentido = -1;
      }
      currentState = GIRAR_OBSTACULOS;
      giraObstaculos();
      break;
    

    case GIRAR_OBSTACULOS:
      Serial.print("encoder ");
      Serial.println(dEncoder);
      vueltas++;
      resetEncoder();
      Serial.println(vueltas);
      if (vueltas >= turns) {
        currentState = AVANCE_FINAL_OBSTACULOS;
        Serial.println("AVANCE_FINAL_OBSTACULOS");
      } else {
        currentState = ESQUIVA_OBSTACULOS;
        Serial.println("ESQUIVA_OBSTACULOS");
        obstaculo = 'Y';
      }
      break;
    
    case ESQUIVA_OBSTACULOS:
      if (obstaculo=='Y'){
        desifrarMensaje();
      } else {
        controlMotor(1);
        if (obstaculo=='R'){
          girarServo(1);
          delay(1000);
          girarServo(-1);
          delay(1000);
          girarServo(0);

        }
        if (obstaculo=='V'){
          girarServo(-1);
          delay(1000);
          girarServo(1);
          delay(1000);
          girarServo(0);

        }
        if (obstaculo=='N'){
          currentState = AVANZAR_OBSTACULOS;
        }
      }
      break;

    case AVANCE_FINAL_OBSTACULOS:
      controlMotor(1);
      girarServo(0);
      if (dEncoder > 50) {
        currentState = DETENERSE_OBSTACULOS;
        Serial.println("DETENERSE_OBSTACULOS");
      }
      break;
      
    case DETENERSE_OBSTACULOS:
      controlMotor(0);
      break;
  }
}

void desifrarMensaje(){
  if (Serial.available()) {
    String mensaje = Serial.readStringUntil('\n'); 
    if (mensaje[0] == 'V') obstaculo = 'V';
    if(mensaje[0] == 'R') obstaculo = 'R';
  }
}

void giraObstaculos(){
  controlMotor(0);
  girarServo(sentido);
  delay(2000);
  controlMotor(1);
  delay(2100);
  resetEncoder();
  currentState = ESQUIVA_OBSTACULOS;
  Serial.println("ESQUIVAR_OBSTACULOS");
}

void giraAbierta(){
  currentState = GIRAR_ABIERTA;
  Serial.println("GIRAR_ABIERTA");
  controlMotor(0);
  girarServo(sentido);
  delay(2000);
  controlMotor(1);
  delay(2100);
  resetEncoder();
}

int anterior= 253235;
// ==================== SERVO ====================
void girarServo(int i) {
  if(i==anterior) return;
  anterior = i;
  Serial.print("S");   // Enviar a Raspberry
  Serial.println(i);
}

// ==================== MOTOR ====================
void setupMotor() {
  pinMode(PIN_IN1A, OUTPUT);
  pinMode(PIN_IN2A, OUTPUT);
  pinMode(PIN_PWMA, OUTPUT);
  pinMode(PIN_STBY, OUTPUT);
  digitalWrite(PIN_STBY, HIGH);
}

void controlMotor(int i) {
  int velocidad = 0;
  switch (i) {
    case -1:
      analogWrite(PIN_PWMA, VELOCIDAD_NORMAL);
      digitalWrite(PIN_IN1A, LOW);
      digitalWrite(PIN_IN2A, HIGH);
      return;
    case 0:
      digitalWrite(PIN_IN1A, LOW);
      digitalWrite(PIN_IN2A, LOW);
      return;
    case 1: velocidad = 100; break;
    case 2: velocidad = 130; break;
    case 3: velocidad = 160; break;
    case 4: velocidad = 190; break;
    case 5: velocidad = 220; break;
    case 6: velocidad = 255; break;
    default: velocidad = VELOCIDAD_NORMAL; break;
  }
  analogWrite(PIN_PWMA, velocidad);
  digitalWrite(PIN_IN1A, HIGH);
  digitalWrite(PIN_IN2A, LOW);
}

// ===== BOTONES =====
void setupBotones() {
  pinMode(PIN_BOTON_VERDE, INPUT_PULLUP);
  pinMode(PIN_BOTON_AZUL, INPUT_PULLUP);
}
void BotonVerdePresionado() {
  if (digitalRead(PIN_BOTON_VERDE) == LOW) {
    BV = true;
  }
}
void BotonAzulPresionado() {
  if (digitalRead(PIN_BOTON_AZUL) == LOW) {
    BA = true;
  }
}

// ==================== ULTRASONICOS ====================
void setupUltrasonicos() {
  pinMode(PIN_TRIG_FRENTE, OUTPUT);
  pinMode(PIN_ECHO_FRENTE, INPUT);
  pinMode(PIN_TRIG_DER, OUTPUT);
  pinMode(PIN_ECHO_DER, INPUT);
  pinMode(PIN_TRIG_IZQ, OUTPUT);
  pinMode(PIN_ECHO_IZQ, INPUT);
}

float leerUltrasonico(int trigPin, int echoPin) {
  unsigned long pingTime;
  float distance;
  digitalWrite(trigPin, HIGH);
  delayMicroseconds(10);
  digitalWrite(trigPin, LOW);
  pingTime = pulseIn(echoPin, HIGH, timeOut);
  distance = (float)pingTime * soundVelocity / 2 / 10000;
  return distance;
}

unsigned long lastUpdate = 0;
const unsigned long interval = 30; // cada 30 ms ≈ 33 Hz

void actualizarDistancias() {
  /*
  if (dF > 0) dfFrente = dF;
if (dD > 0) dfDer = dD;
if (dI > 0) dfIzq = dI;
  */
  if (millis() - lastUpdate < interval) return; // aún no toca actualizar
  lastUpdate = millis();
  
  // Lecturas en bruto
  float dF = leerUltrasonico(PIN_TRIG_FRENTE, PIN_ECHO_FRENTE);
  float dD = leerUltrasonico(PIN_TRIG_DER, PIN_ECHO_DER);
  float dI = leerUltrasonico(PIN_TRIG_IZQ, PIN_ECHO_IZQ);

  // Si la lectura es válida (no cero), aplica el filtro; si no, conserva el valor anterior
  if (dF > 0) dfFrente = alpha * dF + (1 - alpha) * dfFrente;
  if (dD > 0) dfDer = alpha * dD + (1 - alpha) * dfDer;
  if (dI > 0) dfIzq = alpha * dI + (1 - alpha) * dfIzq;

  // Encoder -> metros (ajusta divisor según tu resolución)
  dEncoder = (float)posEncoder / 39.0;
}


void mostrarDistancias() {
  Serial.print(dfFrente, 2); Serial.print("\t");
  Serial.print(dfDer, 2); Serial.print("\t");
  Serial.print(dfIzq, 2); Serial.print("\t");
  Serial.println(dEncoder);
}

// ==================== ENCODER ====================
void setupEncoder() {
  pinMode(PIN_ENCA, INPUT);
  pinMode(PIN_ENCB, INPUT);
  attachInterrupt(digitalPinToInterrupt(PIN_ENCA), readEncoder, RISING);
}

void readEncoder() {
  int b = digitalRead(PIN_ENCB);
  if (b > 0) posEncoder++;
  else posEncoder--;
}

void resetEncoder() {
  posEncoder = 0;
  dEncoder = 0;
}

void pruebaAbierta(){
  
}

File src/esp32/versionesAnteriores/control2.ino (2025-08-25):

#include <Wire.h>
#include <MPU6050.h>  
#include "I2Cdev.h"  
#include "math.h"

//IMU
MPU6050 accelgyro;

int16_t ax, ay, az;  
int16_t gx, gy, gz;
double angleA1, angleA2; 
double angleG1, angleG2; 
double angleC1, angleC2; 

//MOTOR
const int PIN_PWMA = 25;
const int PIN_IN1A = 27;
const int PIN_IN2A = 26;
const int PIN_STBY = 14;

//ENCODER LO VOY DEJAR ASI NOMAS POR MIENTRAS
const int PIN_ENCA = 5;
const int PIN_ENCB = 4;

//BOTONES
const int PIN_BOTON_VERDE = 12;
const int PIN_BOTON_AZUL = 13;

//ULTRASONICO
const int PIN_TRIG = 32; // define PIN_TRIG
const int PIN_ECHO = 33; // define PIN_ECHO.
#define MAX_DISTANCE 700 // Maximum sensor distance is rated at 400-500cm.
//timeOut= 2*MAX_DISTANCE /100 /340 *1000000 = MAX_DISTANCE*58.8
float timeOut = MAX_DISTANCE * 60; 
int soundVelocity = 340; // define sound speed=340m/s


int posEncoder = 0; //posicion del encoder

int E = 0 , B = 0 , M = 0 , U = 0 , I = 0 , S = 0; //valores de los mensajes


const int VELOCIDAD_NORMAL = 250;

void setup() {
  // put your setup code here, to run once:
  Serial.begin(9600);
  setupMotor();
  setupEncoder();
  setupBotones();
  setupUltrasonico();
  setupIMU();
}

void loop() {
  desifrarMensaje();
}

void desifrarMensaje(){
  // Mensajes           Pueden estar en true o false
  //                                     1      0
  //  Encoder       E
  //  Botones       B
  //  Motor         M
  //  IMU           I
  //  Ultrasonico   U
  if (Serial.available()) { // Si hay datos recibidos
    String mensaje = Serial.readStringUntil('\n'); // Lee hasta salto de línea
    //Serial.print("Recibido: ");
    //Serial.println(mensaje); // Responde por serial
    if (mensaje[0]=='M'){
      if (mensaje[1]=='1') {
        M=1;
        //Serial.println("Motor avanza");
      }
      else M=0;
    } else if (mensaje[0]=='E'){
      if (mensaje[1]=='1') E= 1;
      else E=0;
    } else if (mensaje[0]=='B'){
      if (mensaje[1]=='1') B= 1;
      else B=0;
    } else if (mensaje[0]=='S'){
      if (mensaje[1]=='1') S= 1;
      else S=0;
    } else if (mensaje[0]=='U'){
      if (mensaje[1]=='1') U= 1;
      else U=0;
    } else if (mensaje[0]=='I'){
      if (mensaje[1]=='1') I= 1;
      else I=0;
    }
  }

  if (M == 1){
    avanzar();
  } else if (M == 0){
    detenerse();
  }
  if (E == 1) imprimePosEncoder();
  if (B == 1) botonesPresionados();
  if (U == 1) mostrarDistancia();
  if (I == 1) {
    accelgyro.getMotion6(&ax, &ay, &az, &gx, &gy, &gz);
    anguloGiroscopio();
    delay(100);  
  }

}

//MOTOR
void setupMotor() {
  pinMode(PIN_IN1A, OUTPUT);
  pinMode(PIN_IN2A, OUTPUT);
  pinMode(PIN_PWMA, OUTPUT);
  pinMode(PIN_STBY, OUTPUT);
  digitalWrite(PIN_STBY, HIGH);
}

void setMotor(int dir, int pwmVal) {
  analogWrite(PIN_PWMA, pwmVal);
  if (dir == 1) {
    digitalWrite(PIN_IN1A, HIGH);
    digitalWrite(PIN_IN2A, LOW);
  } else if (dir == -1) {
    digitalWrite(PIN_IN1A, LOW);
    digitalWrite(PIN_IN2A, HIGH);
  } else {
    digitalWrite(PIN_IN1A, LOW);
    digitalWrite(PIN_IN2A, LOW);
    //digitalWrite(PIN_STBY, LOW);
  }
}

void avanzar() {
  analogWrite(PIN_PWMA, VELOCIDAD_NORMAL);
  digitalWrite(PIN_IN1A, HIGH);
  digitalWrite(PIN_IN2A, LOW);
}

void reversa() {
  analogWrite(PIN_PWMA, VELOCIDAD_NORMAL);
  digitalWrite(PIN_IN1A, LOW);
  digitalWrite(PIN_IN2A, HIGH);
}

void detenerse() {
  digitalWrite(PIN_IN1A, LOW);
  digitalWrite(PIN_IN2A, LOW);
}


//ENCODER
void setupEncoder(){
  pinMode(PIN_ENCA, INPUT);
  pinMode(PIN_ENCB, INPUT);
  attachInterrupt(digitalPinToInterrupt(PIN_ENCA), readEncoder, RISING);
}

void readEncoder(){
  int b= digitalRead(PIN_ENCB);
  if (b>0){
    posEncoder++;
  } else {
    posEncoder--;
  }
}

void imprimePosEncoder(){
  Serial.println(posEncoder);
}

//BOTONES
void setupBotones() {
  pinMode(PIN_BOTON_VERDE, INPUT_PULLUP);
  pinMode(PIN_BOTON_AZUL, INPUT_PULLUP);
}

void botonesPresionados(){
  if (BotonVerdePresionado()) {
    Serial.println("Boton verde presionado");
  }
  if (BotonAzulPresionado()) {
    Serial.println("Boton azul presionado");
  }
}

bool BotonVerdePresionado() {
  static int lastStableState = HIGH;
  static int lastButtonState = HIGH;
  static unsigned long lastDebounceTime = 0;
  const unsigned long debounceDelay = 50;
  
  int reading = digitalRead(PIN_BOTON_VERDE);
  bool buttonPressed = false;
  
  // Verificar si el estado cambió (ruido o pulsación real)
  if (reading != lastButtonState) {
    lastDebounceTime = millis();
  }
  
  // Actualizar el último estado
  lastButtonState = reading;
  
  // Si ha pasado el tiempo de debounce
  if ((millis() - lastDebounceTime) > debounceDelay) {
    // Verificar si el estado estable cambió
    if (reading != lastStableState) {
      lastStableState = reading;
      
      // Detectar flanco de bajada (botón presionado)
      if (lastStableState == LOW) {
        buttonPressed = true;
      }
    }
  }
  
  return buttonPressed;
}

bool BotonAzulPresionado() {
  static int lastStableState = HIGH;
  static int lastButtonState = HIGH;
  static unsigned long lastDebounceTime = 0;
  const unsigned long debounceDelay = 50;
  
  int reading = digitalRead(PIN_BOTON_AZUL);
  bool buttonPressed = false;
  
  // Verificar si el estado cambió (ruido o pulsación real)
  if (reading != lastButtonState) {
    lastDebounceTime = millis();
  }
  
  // Actualizar el último estado
  lastButtonState = reading;
  
  // Si ha pasado el tiempo de debounce
  if ((millis() - lastDebounceTime) > debounceDelay) {
    // Verificar si el estado estable cambió
    if (reading != lastStableState) {
      lastStableState = reading;
      
      // Detectar flanco de bajada (botón presionado)
      if (lastStableState == LOW) {
        buttonPressed = true;
      }
    }
  }
  
  return buttonPressed;
}

void mostrarDistancia(){
  delay(100); // Wait 100ms between pings (about 20 pings/sec).
  //Serial.print("Ultrasonico: "); 
  //Serial.printf("Distance -> ");
  Serial.println(UltrasonicoLoop()); // Send ping, get distance in cm and print result 
  //Serial.println("cm");
}

void setupUltrasonico(){
  pinMode(PIN_TRIG,OUTPUT);// set PIN_TRIG to output mode
  pinMode(PIN_ECHO,INPUT); // set PIN_ECHO to input mode
}

float UltrasonicoLoop() {
  unsigned long pingTime;
  float distance;
  // make PIN_TRIG output high level lasting for 10μs to triger HC_SR04
  digitalWrite(PIN_TRIG, HIGH); 
  delayMicroseconds(10);
  digitalWrite(PIN_TRIG, LOW);
  // Wait HC-SR04 returning to the high level and measure out this waitting time
  pingTime = pulseIn(PIN_ECHO, HIGH, timeOut); 
  // calculate the distance according to the time
  distance = (float)pingTime * soundVelocity / 2 / 10000; 
  return distance; // return the distance value
}

void setupIMU(){
  Wire.begin();   
  accelgyro.initialize();
}
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

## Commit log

2025-04-29 probando el robot
2025-06-23 Modelo del adaptador del motor
    [Copy of Lego Technic Axle 7 1.stl]
2025-07-20 funciona el link?
2025-07-22 info de los componentes
2025-07-22 borrando cosas de mas
2025-07-23 Tabla de contenidos
2025-07-24 detalles con el step down
2025-08-16 ajustes de componentes
2025-08-24 explicando mas sobre la competendia, arreglando detalles del hardware
2025-08-25 visualizar modelos 3d
    [Copy of Lego Technic Axle 7 1.stl, ENSAMBLE FINAL - CLAVO 17 MM-1.STL, ENSAMBLE FINAL - CLAVO 17 MM-2.STL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]
2025-08-25 Actualizacion de codigo
2025-08-26 Descripcion de esquemas
2025-09-01 Modelos sin hoyos jeje
    [ADAPTADOR LEGO LLANTA STEREN.STL, BASE PARA CAMARA.STL, ENSAMBLE DE PIEZA MEDIO.STL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]
2025-09-16 actualizacion del codigo del esp32
2025-09-17 esquema del circuito electrico
    [prueba2.fzz]
2025-09-18 reporte de costos
2025-09-20 actualizacion de md de carpetas
